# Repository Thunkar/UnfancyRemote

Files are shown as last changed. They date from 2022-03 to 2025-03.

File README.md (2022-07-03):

# The Unfancy Remote

A cheap, open, modular and reliable DIY remote with a focus on RF performance. 

**WARNING** : The software and CAD files included in this repo are in a **BETA STAGE** at the moment and **SHOULD BE USED CAREFULLY**. I am not responsible for **ANY** injures or damages you may incur as a result of using the HW or SW described in this project.

# Design considerations

* Unfancy. I use other devices for my telemetry, so no UART (even though could be easily added in the future) or OLED screens. PPM for the win.
* DIY friendly and modular. 
* Stellar RF performance is a must. The whole idea for this project came after in the FPV drone space [this project](https://www.expresslrs.org/2.0/) became super popular. It uses LoRa transcievers to achieve great range and link speeds, using a proprietary modulation that is specially robust against interference. It can also work on 433MHz/868MHz/2.4GHz bands depending on the specific module.
* Multiple shells to accomodate thumbwheels, triggers, Qi charging, battery sizes...
* Community driven

# Building the code

It has been tested on the latest (at the time of writing, 1.8.19) Arduino IDE version, using the fantastic [SX12XX Library](https://github.com/StuartsProjects/SX12XX-LoRa) by StuartsProjects.

# Documentation

1) [Ordering](./docs/ordering.md)
2) [Soldering](./docs/soldering.md)
3) [Assembly](./docs/assembly.md)
4) [Software configuration](./docs/software.md)
5) [Remote operation](./docs/operation.md)

# Contributing

All contributions must go through a process of review and validation via a Pull Request before being integrated into the codebase. If you wish to contribute, please fork the repo, perform your modifications **TEST THEM** and submit a PR for review. The place to discuss bugs, new features or suggestions is the [esk8 news forum](https://forum.esk8.news/t/the-unfancy-remote-wip-diy-reliable-remote).

# License 
```
            DO WHAT THE FUCK YOU WANT TO PUBLIC LICENSE
                    Version 2, December 2004
 
 Copyright (C) 2022 Gregorio Juliana Quirós
  Madrid, Spain
 Everyone is permitted to copy and distribute verbatim or modified
 copies of this license document, and changing it is allowed as long
 as the name is changed.
 
            DO WHAT THE FUCK YOU WANT TO PUBLIC LICENSE
   TERMS AND CONDITIONS FOR COPYING, DISTRIBUTION AND MODIFICATION
 
  0. You just DO WHAT THE FUCK YOU WANT TO.
  ```

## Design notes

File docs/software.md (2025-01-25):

# Software configuration

## Download the Arduino software and required library

In order to do that, go to https://www.arduino.cc/en/software and get the appropriate version for your OS. Then, navigate to [this repo](https://github.com/StuartsProjects/SX12XX-LoRa) and download it as a `.zip` file:

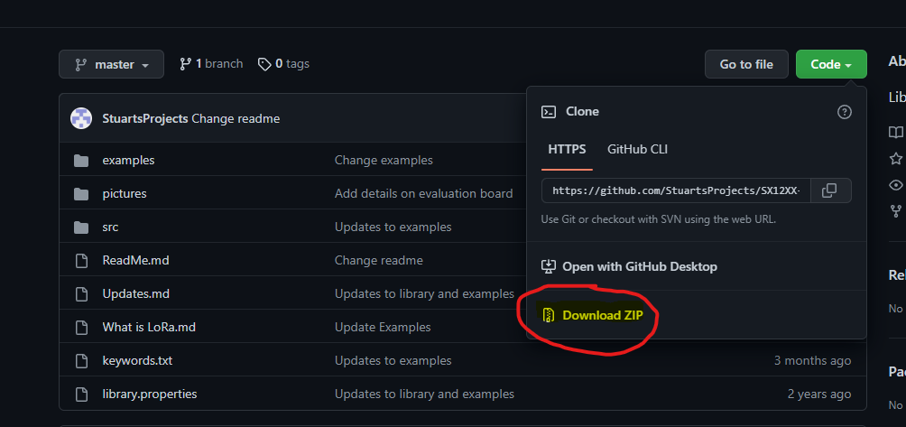
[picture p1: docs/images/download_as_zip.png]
Download as zip


Once you have it secured, import it in your arduino environment using the option `sketch->include library->add .zip library`

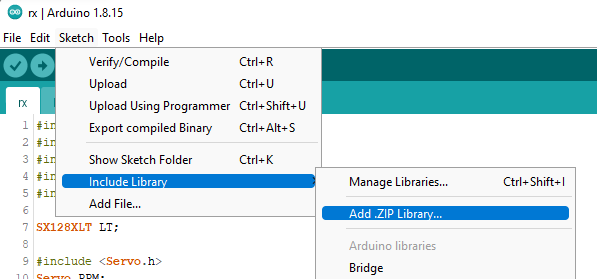
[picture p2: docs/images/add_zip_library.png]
Include zip library


Do the same for https://github.com/ednieuw/ESPAsyncWebServer.git

## Installing drivers for the USB-to-serial converter

If you're using windows, chances are you'll need to install [these drivers](https://ftdichip.com/drivers/)

## Configuring and flashing your transmitter

Download this repository using the same option you used to download the library. Once you have it unzipped, navigate to `software/tx`. The only file that should be modified in 99% of cases is `settings.h`. Configuration options are explained here:

```c
//#define DUAL_THROTTLE <- Uncomment this line if you're using a dual trigger case with 2 sensors.

// In case a dual trigger remote is used, the following line adjusts the sensitivity of the brakes, or in other words, when does the brake lever overrules the throttle. It is NOT recommended to lower it, but it can be raised to prevent accidental brake activation

#ifdef DUAL_THROTTLE
const float BRAKE_SENSITIVITY = 5; 
#endif

// Pairing: Choose a channel (0-40) and a transmitter identity (0-254) to prevent collisions with nearby remotes or other LoRa devices. These numbers must match the receiver's.

const unsigned int channel = -1;
const unsigned int TXIdentity = -1; 

// Battery levels: VREF is the actual internal reference of the Arduino, that can differ from one board to another. It can be adjusted here, increasing this number if the battery is reading high or decreasing it if it's reading low. It is strongly encouraged to use a multimeter to verify the actual values.

const unsigned long VREF = 1148566;

// Battery thresholds: Define what each LED of the remote means in terms of cell voltage, both for the remote and the board. First level is 4 LEDs ON, second one 3, etc. The last level will make the remote rumble and the last LED blink. WARNING: a maximum board voltage of 12S (50.4V) is measurable.

const float REMOTE_BATTERY_CELL_V_THR[] = { 4.0, 3.8, 3.7, 3.5, 3.3 };

const float BOARD_BATTERY_CELL_V_THR[] = { 4.0, 3.8, 3.7, 3.5, 3.3 };
const unsigned int BOARD_CELL_S = 12;

```

Once configured, connect the board to the usb adapter. The 328p based boards use this orientation with the jumper on the 3.3V position:

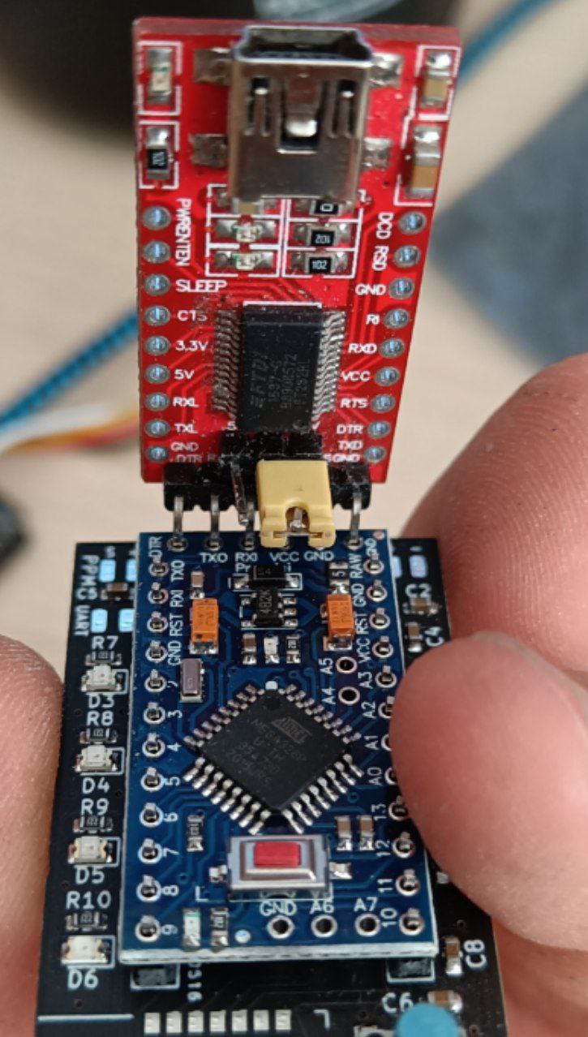
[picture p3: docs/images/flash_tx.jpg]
Flash tx


Select the appropriate board and port in the Arduino IDE:

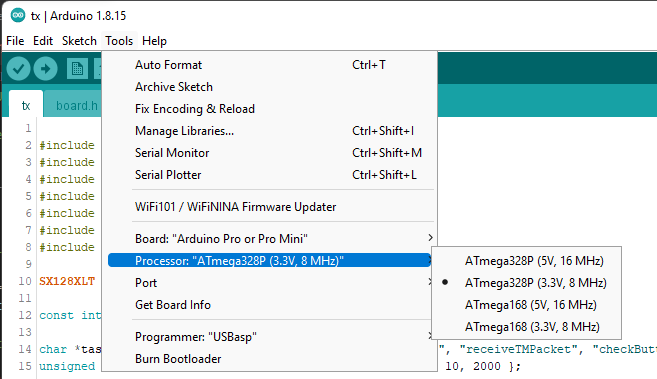
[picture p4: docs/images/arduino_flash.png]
Arduino flash


And upload the code using the upload button (`sketch->upload`). 

## Calibration

If everything worked correctly, the remote should perform the startup routine (rumble + 4 LED on in sequence) and start the calibration routine (1 LED on). To calibrate the remote, follow these steps:

* Don't touch the thumbwheel/triggers to perform center detection. Click the button once.
* Second LED should light up. Push the thumbwheel/acceleration trigger to the maximum acceleration position and let it return to center. Click the button once.
* Third LED should light up. Push the thumbwheel/brake trigger to the maximum braking position and let it return to center. Click the button once.
* The fourth LED should light up and then all of them turn off. Calibration is complete.

After you're finished, it'll start to output debugging information through the serial port running at 115200 baud.

## Configuring and flashing the receiver

Similarly, the receiver has to be configured with matching pairing info:

```c
// Pairing: Choose a channel (0-40) and a transmitter identity (0-254) to prevent collisions with nearby remotes or other LoRa devices. These numbers must match the transmitter's.

const unsigned int channel = -1;
const unsigned int RXIdentity = -1; 

// Battery levels: VREF is the actual internal reference of the Arduino, that can differ from one board to another. It can be adjusted here, increasing this number if the battery is reading high or decreasing it if it's reading low. It is strongly encouraged to use a multimeter to verify the actual values.

const unsigned long VREF = 1148566;
```

And flashed taking into account the board type. Ff you're using a 168 equipped board, chose it accordingly in the IDE and make sure you connect the adapter correctly:

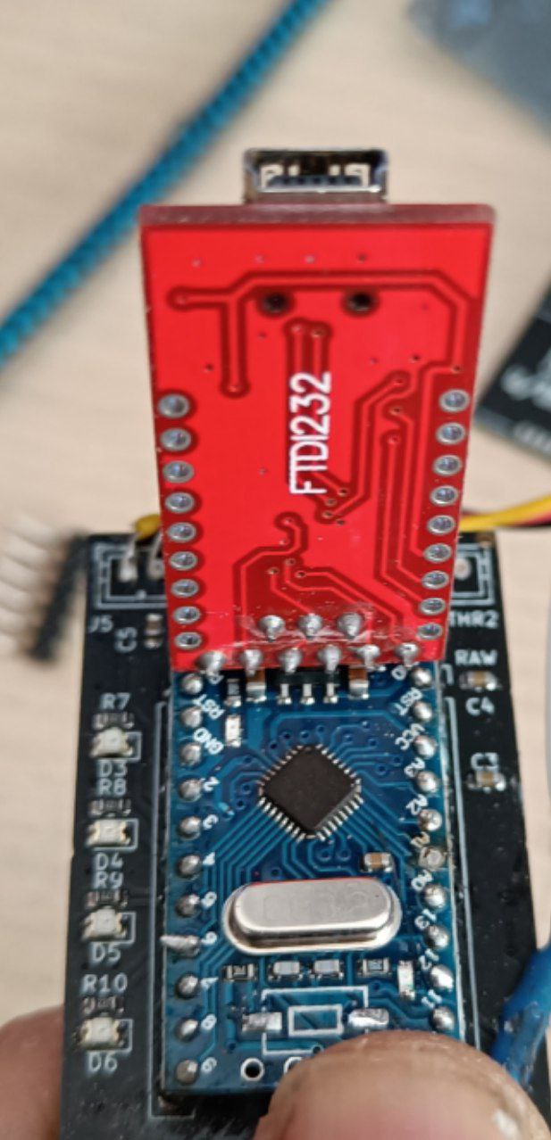
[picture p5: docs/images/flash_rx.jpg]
Flash rx


## Making sure it worked

Turn on the transmitter and connect the receiver to the USB adapter. Using the serial monitor, verify that the receiver is receiving approx. 50 throttle packages per second (usually 47-49) and is emitting 2 TM packages per second (some can be lost, is not a big deal).

## Connecting the receiver to the board

Depending on the ESC you're using the communications port can be arranged in a number of ways, but bear in mind the receiver requires 5V to work. If you want to have battery monitoring for your board in the remote, make sure to take a cable directly from the positive end of your battery and solder it to the VBAT pad in the receiver.

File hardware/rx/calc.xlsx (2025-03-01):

Ref
4.2
Cells | Voltages | R1 | R2 | Max Ouptut | Leakage current (mA)
12 | 50.4 | 100000 | 5600 | 2.672727273 | 0.4772727273
14 | 58.8 | 100000 | 4700 | 2.639541547 | 0.5616045845
16 | 67.2 | 120000 | 4700 | 2.532798717 | 0.538893344
18 | 75.6 | 120000 | 3300 | 2.023357664 | 0.6131386861
20 | 84 | 150000 | 4700 | 2.552036199 | 0.5429864253
22 | 92.4 | 150000 | 3300 | 1.989041096 | 0.602739726

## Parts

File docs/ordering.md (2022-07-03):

# Ordering

## PCBs

Ordering from [JLCPCB](https://jlcpcb.com/) is very easy. First of all, make sure you have successfully downloaded or cloned this repository in your computer, and have unzipped the contents. The first step is to go to the website and click on 'Add gerber file':

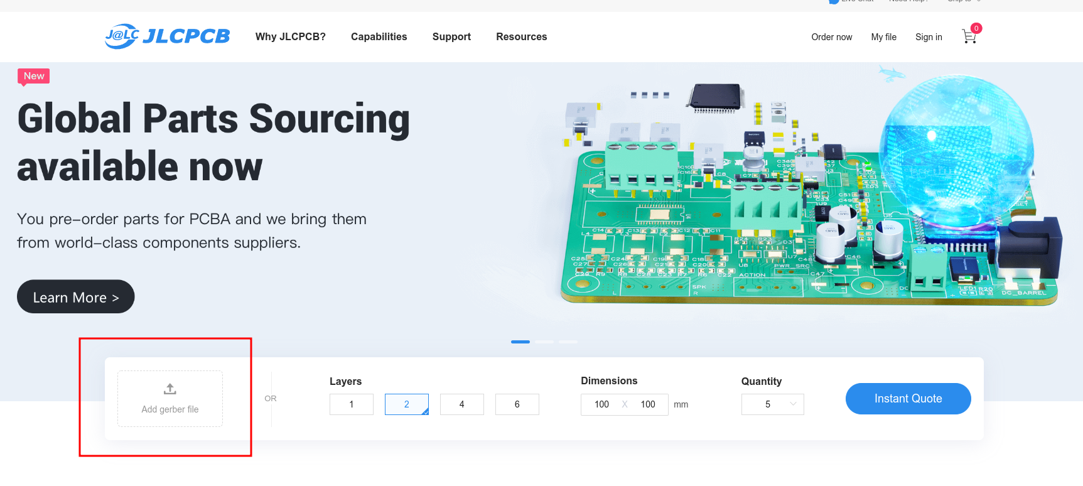
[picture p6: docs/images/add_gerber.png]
Add gerber


Then navigate to `hardware/jlcpcb/gerber` and select `GERBER-unfancyRemote.zip`. These are the design files for the boards that tell the manufacturer exactly how to make them (copper, silkscreen, vias, holes, etc). Once they're loaded and analyzed, you should select the following manufacturing options, except color which you can choose (as long as JLCPB supports SMD assembly in that particular color). The price per remote goes way down if you order 20+ boards, and you need 2 per kit (1 transmitter and 1 receiver, the same PCB can act as both). Get some friends to join your purchase!

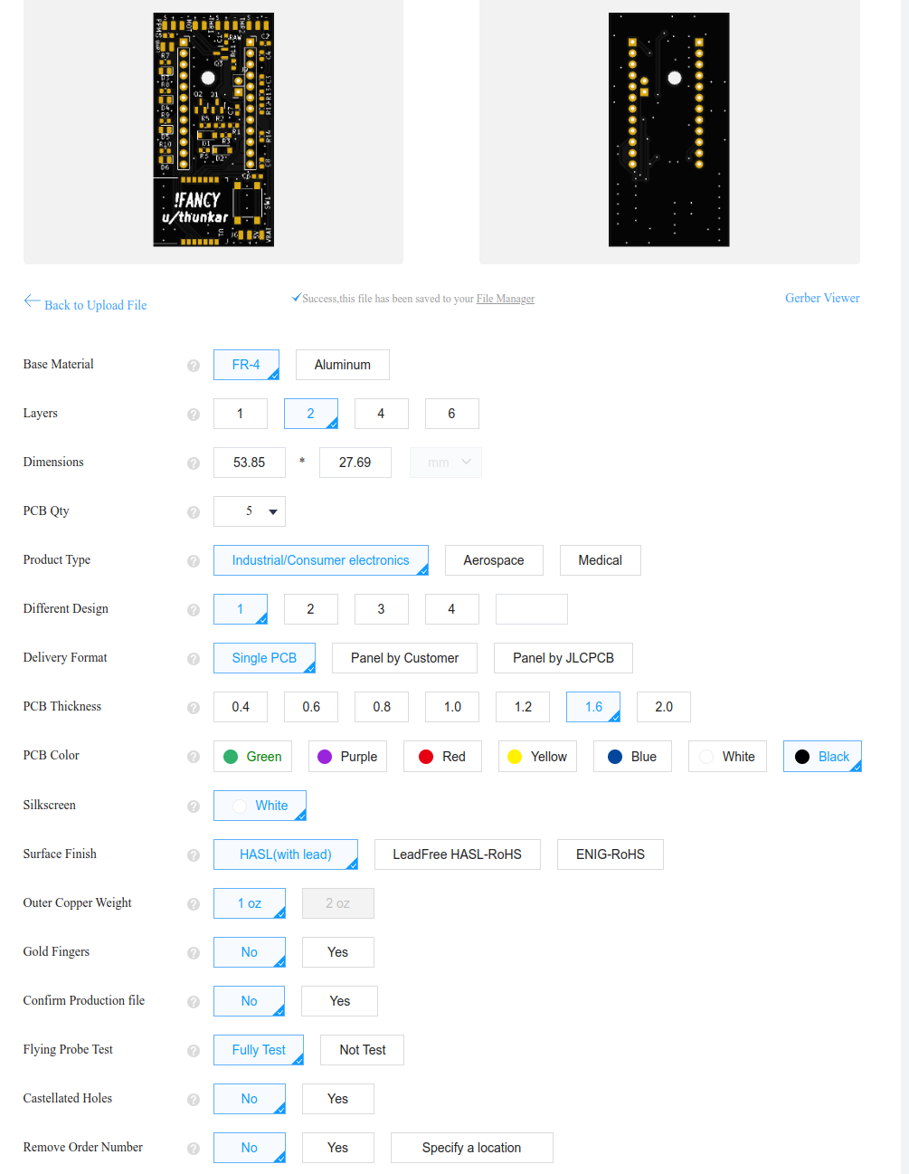
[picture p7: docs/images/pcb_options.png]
PCB options


Select "PCB assembly" and the following options. The PCB only has components on the top side, so manual soldering will be kept to a minimum:

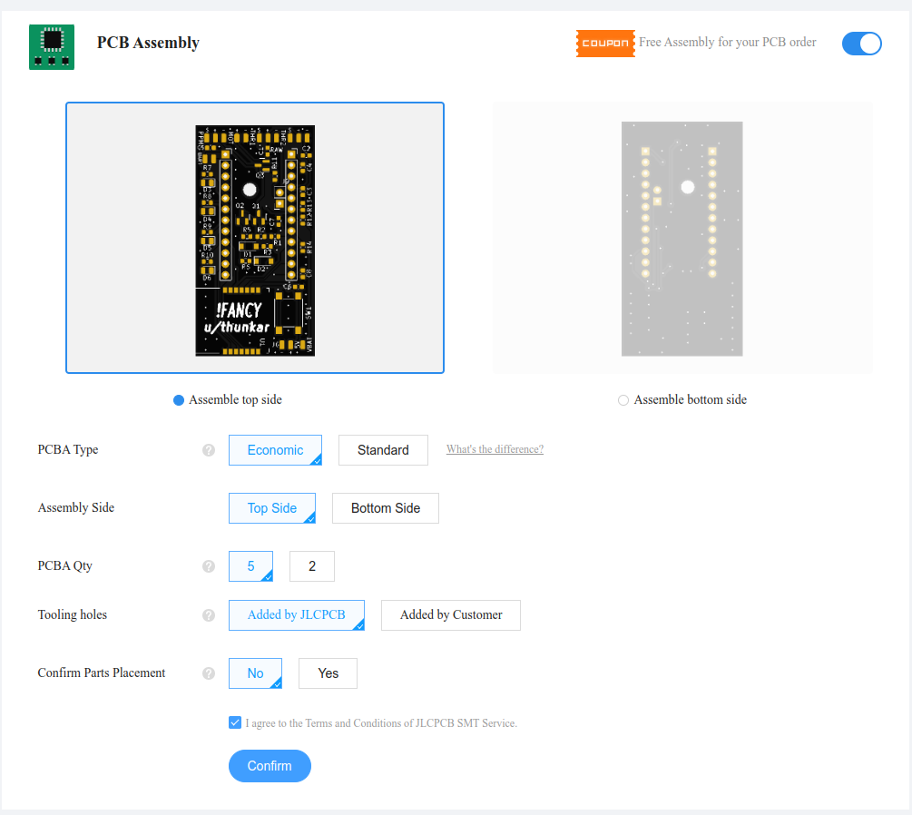
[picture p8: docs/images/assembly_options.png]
PCB assembly


On the next screen, upload the BOM (`hardware/jlcpcb/assembly/BOM-unfancyRemote.csv`) and CPL file (`hardware/jlcpcb/assembly/POS-unfancyRemote.csv`). Select `Research/Education/DIY/Entertainment -> Toy` as category and click next. The component list should appear, leaving only 3 unpopulated parts: Arduino digital, Arduino analog and Extra analog 1. This is fine, you'll solder this when assembling the remote. If there are more components missing, create a [PR](https://github.com/Thunkar/UnfancyRemote/pulls) so we can try and find an alternative.

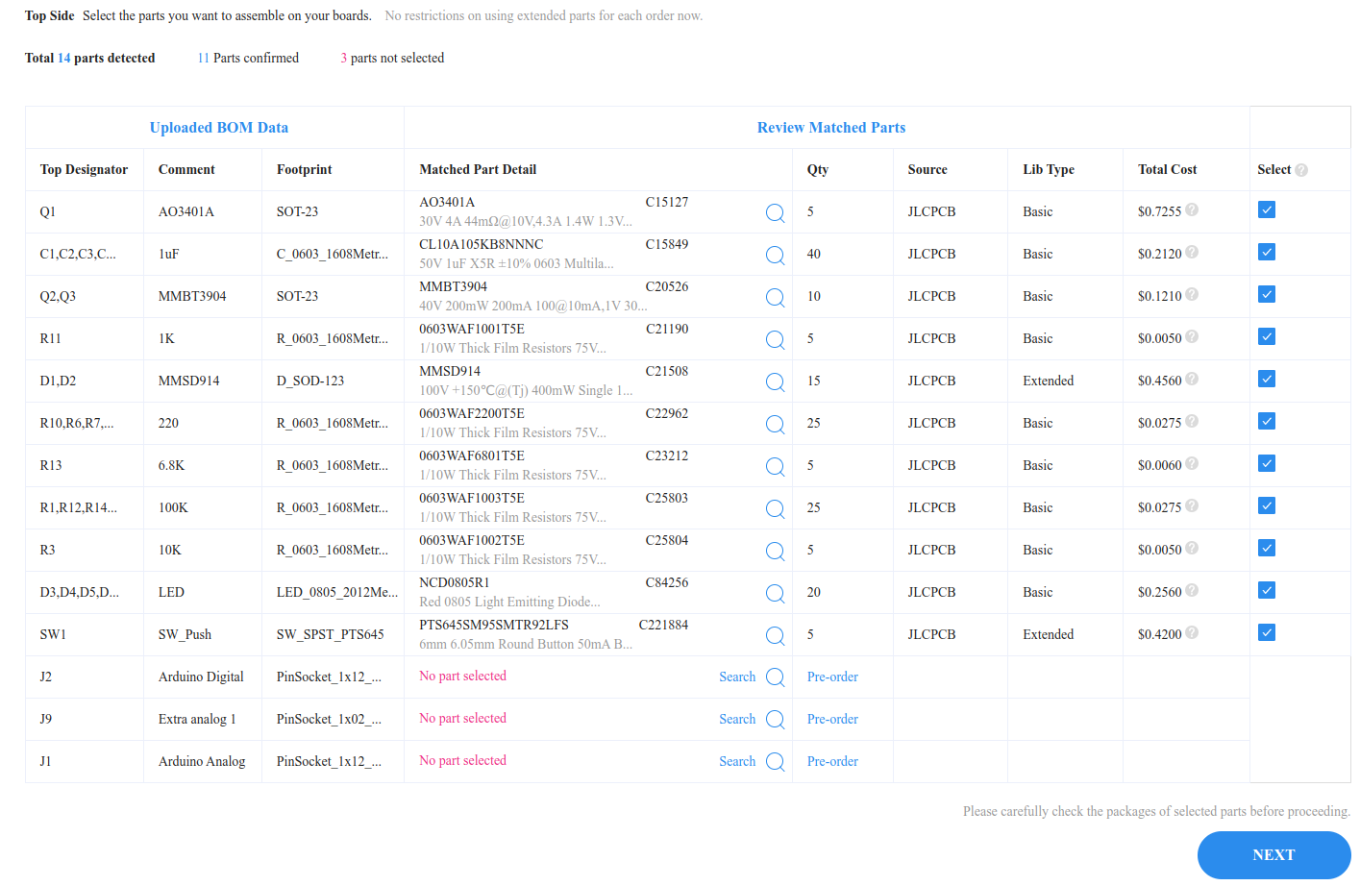
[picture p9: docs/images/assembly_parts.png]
Assembly parts


Next you'll see a summary of your order. Pricing should be around $20 excluding shipping if you select only 5 PCBs, but I do insist that 20 will be less than $50 WITH shipping, so find some mates! In the unselected parts section only headers/connectors and the LoRa module should appear:

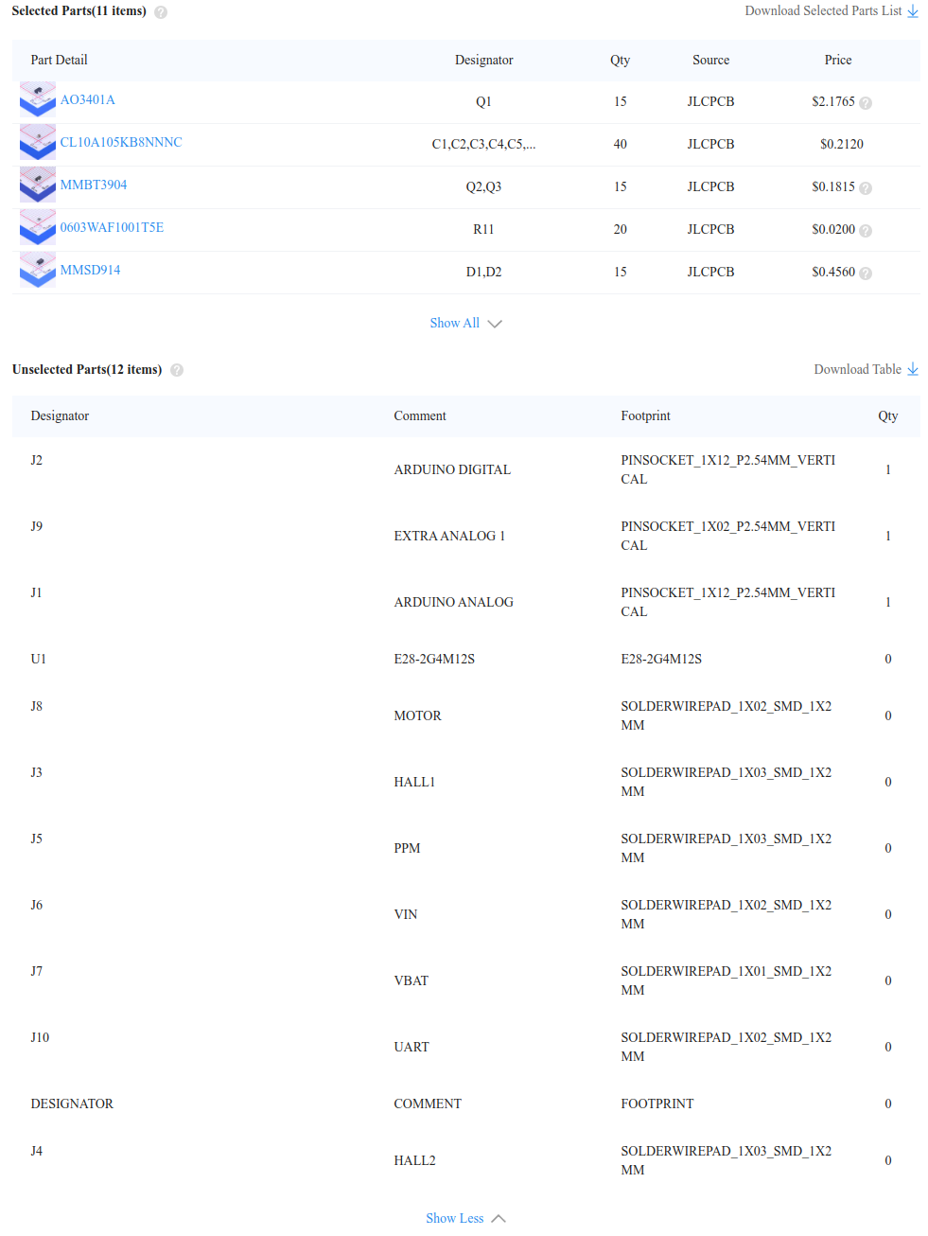
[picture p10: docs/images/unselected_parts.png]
Unselected parts


You're done! Pay for your order and shipping, it should be with you in less than 15 days even with the cheapest option.

## Other components

| Part | Description | Required quantity | Aliexpress | Amazon (ES) |
| --- | --- | --- | --- | --- |
| Springs | 20x5x0.5 (length\*inner diameter\*wire diameter). 0.4/0.6 wire diameter could work for softer/stiffer | 1 (2 for dual trigger) | [Link for 10 springs](https://es.aliexpress.com/item/1005003435808058.html) | [Kit with a lot of springs, not recommended](https://www.amazon.es/gp/product/B01KG024CU/ref=ppx_yo_dt_b_asin_title_o05_s00) |
| E28-2G4M12S SX1280 2.4G LoRa Module | One for the remote, another for the receiver | 2 | [Single module](https://es.aliexpress.com/item/1005003949324557.html) | [Single module](https://es.aliexpress.com/item/1005003949324557.html) |
| Arduino Pro Mini 3.3V 8MHz Atmega 328P | Required for the remote ATM, can be also used in the receiver but it's more expensive | 1 (2 if used also in the receiver) | [Single board](https://es.aliexpress.com/item/4000873049870.html?spm=a2g0o.order_list.0.0.35de194dDIWxKm&gatewayAdapt=glo2esp) | [Single board](https://www.amazon.es/gp/product/B01DUSDQQ8/ref=ppx_yo_dt_b_asin_title_o02_s00?ie=UTF8&psc=1) |
| Arduino Pro Mini 3.3V 8MHz Atmega 168  | Can be used in the receiver as cheaper alternative | 1 (if not using 2x 328P) | [Single board](https://es.aliexpress.com/item/4000873049870.html?spm=a2g0o.order_list.0.0.35de194dDIWxKm&gatewayAdapt=glo2esp) | N/A 
| Serial to USB adapter | Used to upload FW to the Arduino | 1 | [1 board](https://es.aliexpress.com/item/32460118879.html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) | [1 board](https://www.amazon.es/Movilideas-Adaptador-FT232RL-Serie-Arduino/dp/B07H9CXVGK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) |
| LiPo charger | Micro USB, pretty inexpensive | 1 | [10 boards](https://es.aliexpress.com/item/1800678916.html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) | [1-3-5 boards](https://www.amazon.es/gp/product/B07D2G345P/ref=ppx_yo_dt_b_asin_title_o05_s00?ie=UTF8&psc=1) |
| 3.0-4.2 to 5V regulator | From battery voltage to 5V, extremely small (audible coil whine) | 1 | [5 boards](https://es.aliexpress.com/item/4000805939587.html?spm=a2g0o.order_list.0.0.1024194dNATUMn&gatewayAdapt=glo2esp) | N/A |
| LiPo battery | Bought Tattu LiPos a while back and they're good. Cannot vouch for aliexpress ones | 1 | [Pick your poison, any of this size works](https://es.aliexpress.com/item/1005001330075053.html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) | [6 batteries](https://www.amazon.es/gp/product/B07X9XYPP5/ref=ppx_yo_dt_b_asin_title_o09_s00?ie=UTF8&psc=1) |
| Magnets | 4x2 (diameter\*height) N35 neodymium magnets | 2 | [50 pack](https://es.aliexpress.com/item/1005002803855055.html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) | [50 pack](https://www.amazon.es/gp/product/B00TACMJEO/ref=ppx_yo_dt_b_search_asin_title?ie=UTF8&psc=1) |
| Hall sensor | 49E linear hall sensor (SS49E) | 1 (2 for dual trigger) | [10 pack](https://es.aliexpress.com/item/32590021901.html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) | [10 pack](https://www.amazon.es/gp/product/B08LD57DZ6/ref=ppx_yo_dt_b_asin_title_o00_s00?ie=UTF8&psc=1) |
| Bearing | MR148ZZ ball bearing | 1 (2 for dual trigger) | [10 pack](https://es.aliexpress.com/item/32834754915.html?spm=a2g0o.order_list.0.0.35de194dDIWxKm&gatewayAdapt=glo2esp) | N/A |
| Qi Charger | OPTIONAL. But very cool (pick the round antenna, blue PCB version) | 1 | [Single board](https://es.aliexpress.com/item/1005003411188792.html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) | N/A |
| Vibration motor | Technically optional but highly recommended | 1 | [10 motors](https://es.aliexpress.com/item/4000245243914.html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) | [5 motors](https://www.amazon.es/gp/product/B0839H19HY/ref=ppx_yo_dt_b_asin_title_o06_s00?ie=UTF8&psc=1) |
| Lanyard | Any would do, really | 1 | [1 lanyard](https://es.aliexpress.com/item/1005001914422530.html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) | N/A 
| Brass inserts | M3x4 (short) | 6 | [100 pack](https://es.aliexpress.com/item/1005002069529871.html) | [100 pack](https://www.amazon.es/gp/product/B09ZHSGHXD/ref=ppx_yo_dt_b_asin_title_o05_s00?ie=UTF8&th=1) |

I'll try to keep this updated if I find better options. If you do, please open a [PR](https://github.com/Thunkar/UnfancyRemote/pulls)

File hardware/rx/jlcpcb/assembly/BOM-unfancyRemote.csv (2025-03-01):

Comment | Designator | Footprint | LCSC
AO3401A | Q1 | SOT-23 | C15127
1uF | C1,C2,C3,C4,C5,C6,C7,C8 | C_0603_1608Metric | C15849
MMBT3904 | Q2,Q3 | SOT-23 | C20526
1K | R11 | R_0603_1608Metric | C21190
MMSD914 | D1,D2 | D_SOD-123 | C21508
SW_Push | SW1 | SW_SPST_PTS645 | C221884
220 | R10,R6,R7,R8,R9 | R_0603_1608Metric | C22962
6.8K | R13 | R_0603_1608Metric | C23212
100K | R1,R12,R14,R2,R5 | R_0603_1608Metric | C25803
10K | R3 | R_0603_1608Metric | C25804
LED | D3,D4,D5,D6 | LED_0805_2012Metric | C84256
Arduino Digital | J2 | PinSocket_1x12_P2.54mm_Vertical
E28-2G4M12S | U1 | E28-2G4M12S
Arduino Analog | J1 | PinSocket_1x12_P2.54mm_Vertical
VIN | J6 | SolderWirePad_1x02_SMD_1x2mm
HALL1 | J3 | SolderWirePad_1x03_SMD_1x2mm
HALL2 | J4 | SolderWirePad_1x03_SMD_1x2mm
PPM | J5 | SolderWirePad_1x03_SMD_1x2mm
Extra analog 1 | J9 | PinSocket_1x02_P2.54mm_Vertical
Motor | J8 | SolderWirePad_1x02_SMD_1x2mm
VBAT | J7 | SolderWirePad_1x01_SMD_1x2mm
UART | J10 | SolderWirePad_1x02_SMD_1x2mm

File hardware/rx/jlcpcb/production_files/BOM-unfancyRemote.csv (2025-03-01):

Comment | Designator | Footprint | LCSC | Quantity
TPS61085DGK | U4 | VSSOP-8_3x3mm_P0.65mm | C113659 | 1
1K | R11,R16,RT1 | R_0402_1005Metric | C11702 | 3
10uF | C11,C13,C14,C6,C8 | CP_EIA-3216-10_Kemet-I | C119051 | 5
4.7uF | C10,C9 | CP_EIA-3216-10_Kemet-I | C123256 | 2
MCP73871-2AA | U2 | QFN-20-1EP_4x4mm_P0.5mm_EP2.5x2.5mm | C144351 | 1
MMBT3904 | Q2,Q3 | SOT-23 | C20526 | 2
MMSD914 | D1,D2 | D_SOD-123 | C21508 | 2
220 | R6 | R_0402_1005Metric | C25091 | 1
470 | R15,R4,R7 | R_0402_1005Metric | C25117 | 3
100K | R1,R12,R14,R2,R5 | R_0402_1005Metric | C25741 | 5
10K | R17,R3 | R_0402_1005Metric | C25744 | 2
18.2K | R18 | R_0402_1005Metric | C25859 | 1
27K | R20 | R_0402_1005Metric | C284471 | 1
MIC5219-3.3YM5 | U5 | SOT-23-5 | C29613 | 1
100nF | C16 | C_0402_1005Metric | C307331 | 1
SW_Push | SW1 | SW_SPST_PTS645 | C393947 | 1
6.8K | R13 | R_0402_1005Metric | C407725 | 1
150K | RT2 | R_0402_1005Metric | C407748 | 1
D_Schottky | D9 | D_SOD-523 | C413992 | 1
1.6nF | C7 | C_0603_1608Metric | C437532 | 1
68K | R19 | R_0402_1005Metric | C482226 | 1
1uF | C12,C15 | C_0402_1005Metric | C52923 | 2
3.3uH | L1 | L_Cenker_CKCS201610 | C696469 | 1
10K | TH1 | R_0402_1005Metric | C700818 | 1
AO3401A | Q1 | SOT-23 | C700954 | 1
LED | D3,D7,D8 | LED_0805_2012Metric | C84256 | 3
WS2812B | D10,D4,D5,D6 | LED_WS2812B-2020_PLCC4_2.0x2.0mm | C965555 | 4
E28-2G4M12S | U1 | E28-2G4M12S |  | 1
Battery | J1 | PinHeader_1x02_P2.00mm_Vertical |  | 1
VIN | J6 | SolderWirePad_1x02_SMD_1x2mm |  | 1
HALL1/PPM | J3 | SolderWirePad_1x03_SMD_1x2mm |  | 1
HALL2 | J4 | SolderWirePad_1x03_SMD_1x2mm |  | 1
Motor | J8 | SolderWirePad_1x02_SMD_1x2mm |  | 1
ESP32-C3_SUPERMINI | U3 | MODULE_ESP32-C3_SUPERMINI |  | 1

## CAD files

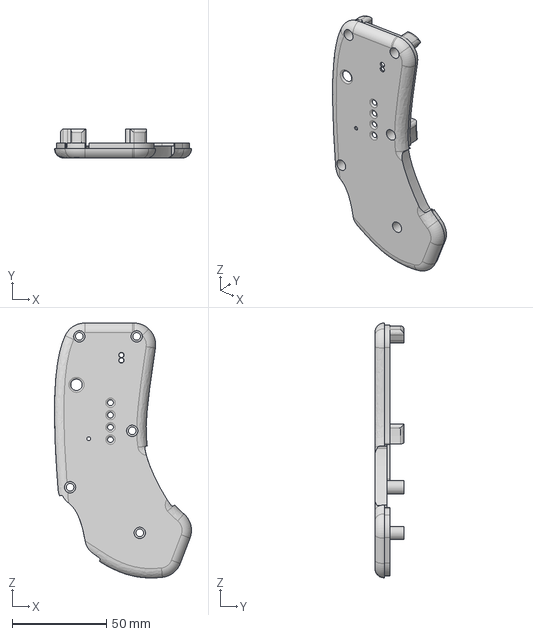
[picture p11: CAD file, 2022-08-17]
cad/dualTrigger/dualTriggerTop.step
72.5 x 15.5 x 134.9 mm

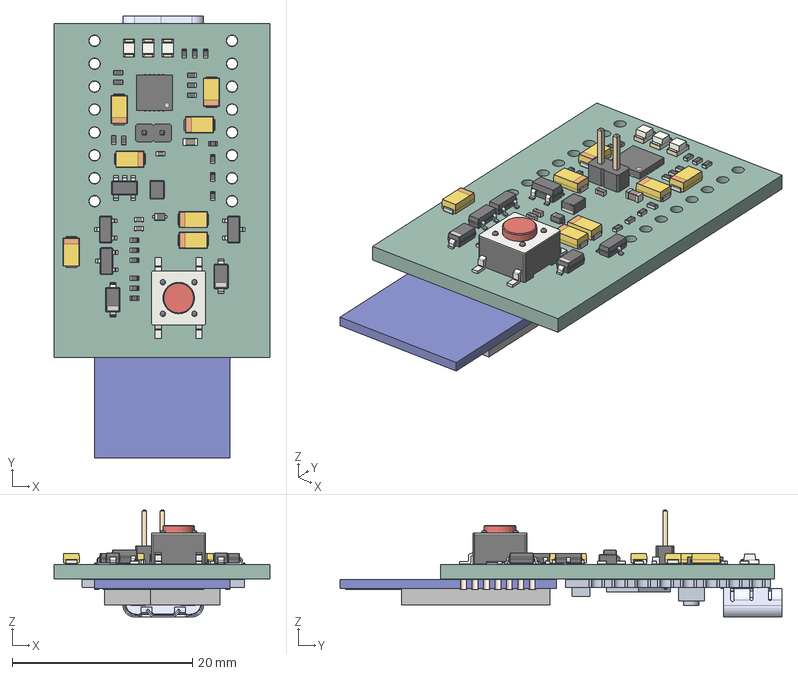
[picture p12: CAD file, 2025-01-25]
cad/misc/PCBv3.step
23.9 x 49.0 x 11.9 mm
R_0402_1005Metric x 20
SOT_23_5
C_0402_1005Metric x 3
CP_EIA_3216_10_Kemet_I x 7
QFN-20-1EP_4x4mm_Pitch0.5mm
L_Cenker_CKCS201610
D_SOD_123 x 2
PinHeader_1x02_P200mm_Vertical
D_SOD_523
LED_0805_2012Metric x 3
SOT_23 x 3
C_0603_1608Metric
SW_SPST_PTS645
E28-2G4M12S v2
ESP32-C3 SuperMini
unfancyRemote_PCB

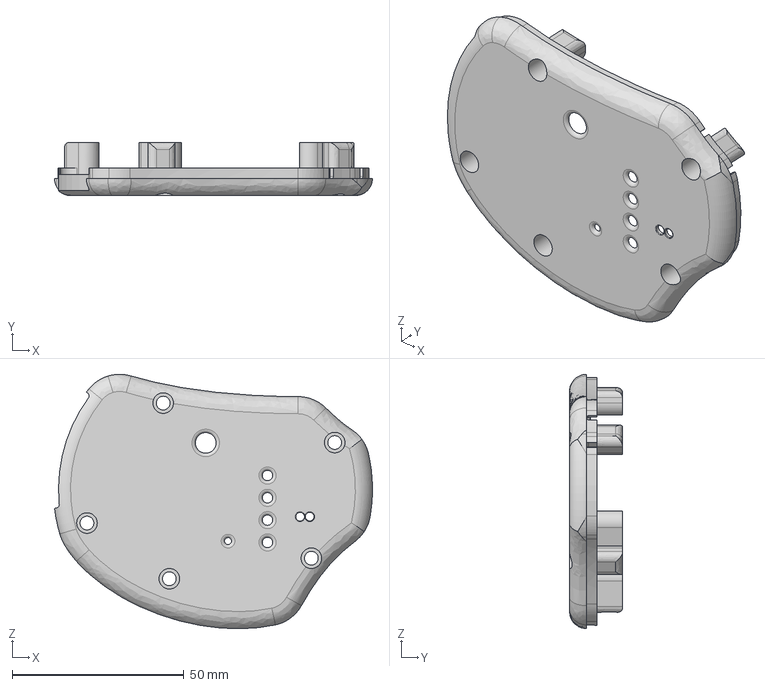
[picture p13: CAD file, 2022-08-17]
cad/round/roundTop.step
92.7 x 15.5 x 74.1 mm

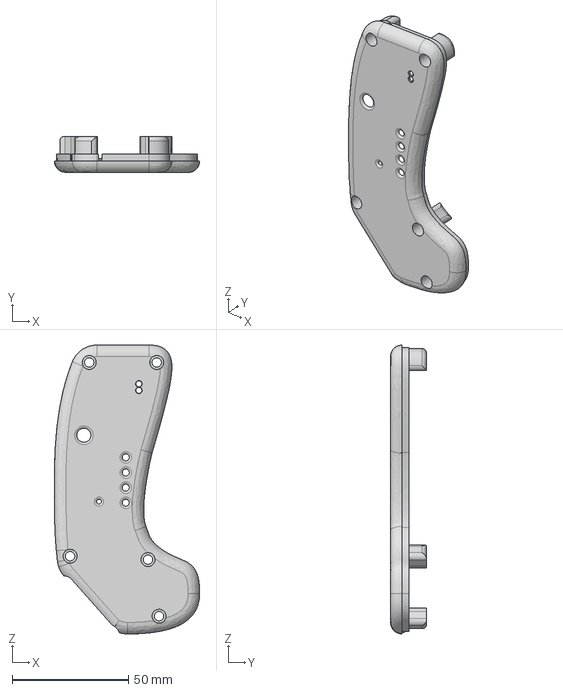
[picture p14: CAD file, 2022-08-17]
cad/thumbwheel/thumbwheelTop.step
62.5 x 15.5 x 124.2 mm

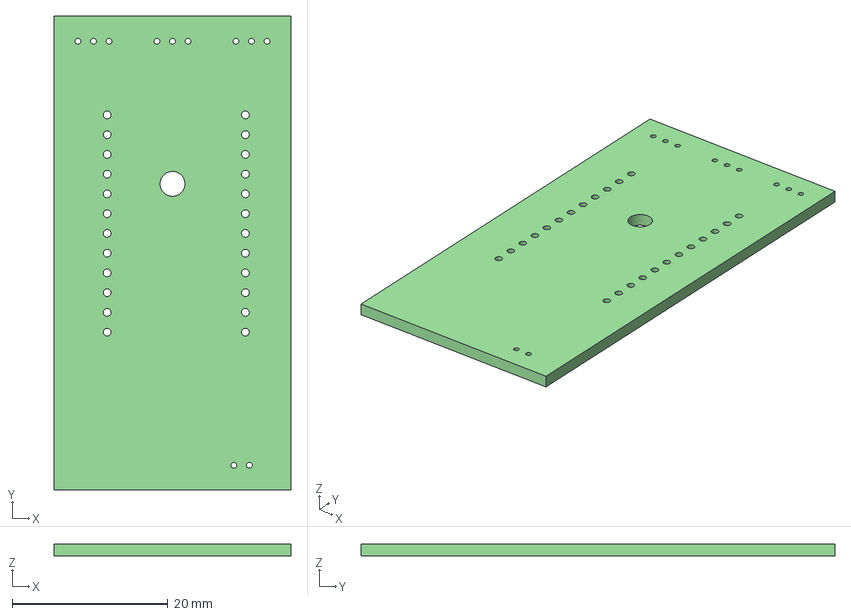
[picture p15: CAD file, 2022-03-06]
hardware/rx/rx.step
30.5 x 61.0 x 1.60 mm

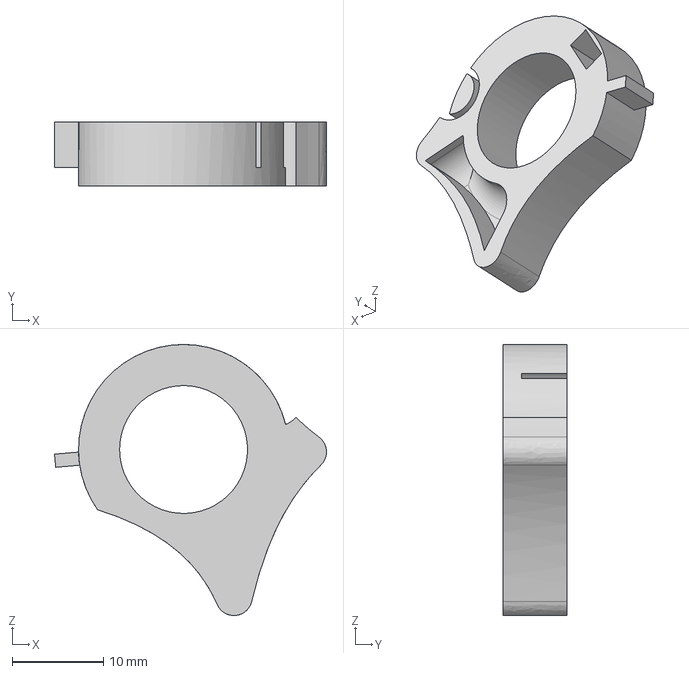
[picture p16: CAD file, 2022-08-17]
cad/dualTrigger/reverseTrigger.step
29.8 x 7.00 x 29.7 mm

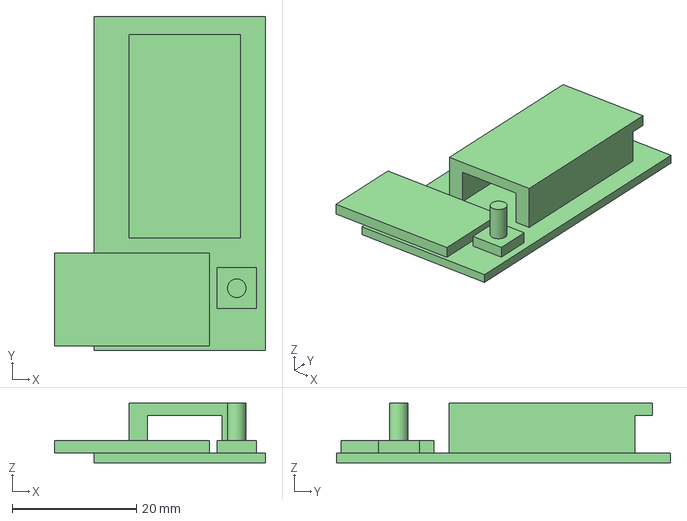
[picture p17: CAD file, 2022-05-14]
cad/misc/PCBv2.step
34.1 x 53.8 x 9.60 mm

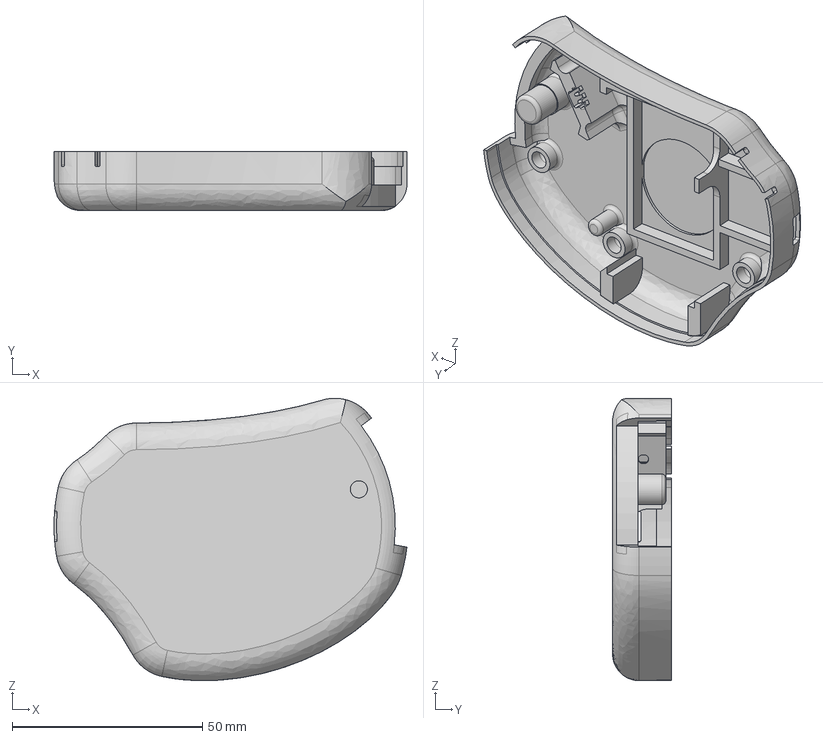
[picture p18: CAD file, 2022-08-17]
cad/round/roundBase.step
92.7 x 15.5 x 74.1 mm

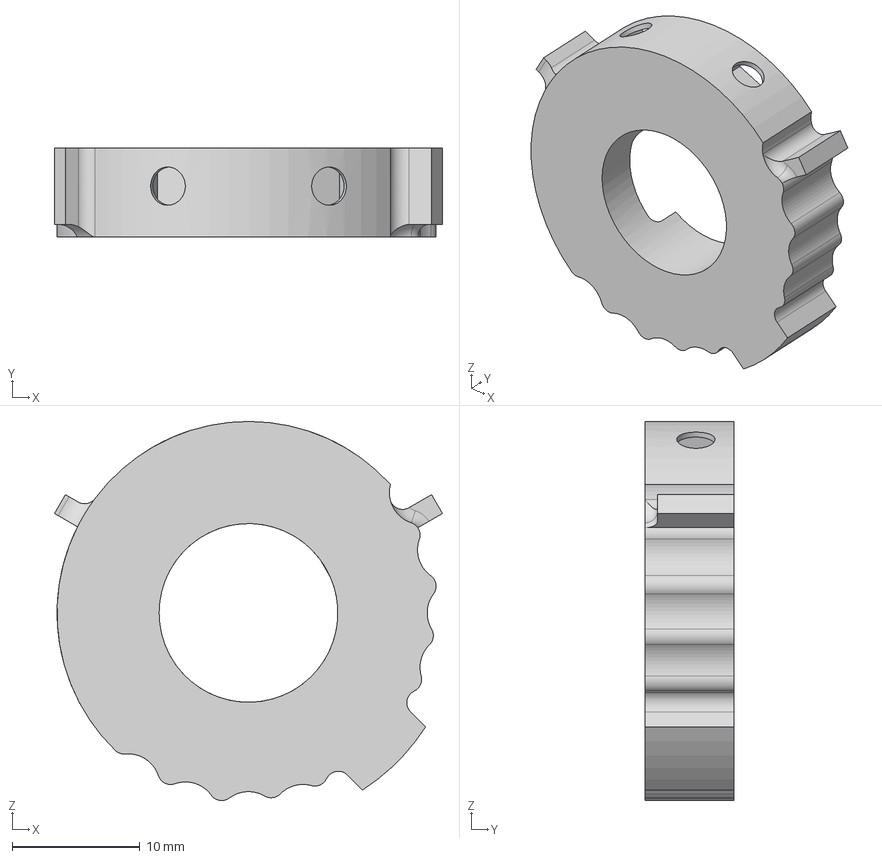
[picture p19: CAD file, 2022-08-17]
cad/thumbwheel/thumbwheelSmall.step
30.4 x 7.00 x 29.7 mm

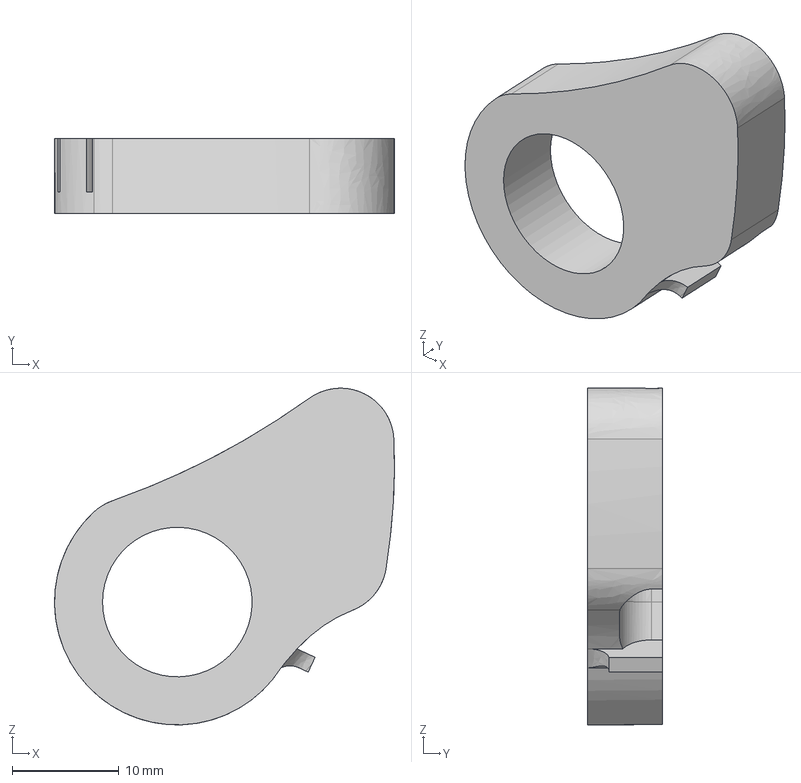
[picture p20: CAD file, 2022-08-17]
cad/dualTrigger/trigger.step
31.8 x 7.00 x 31.5 mm

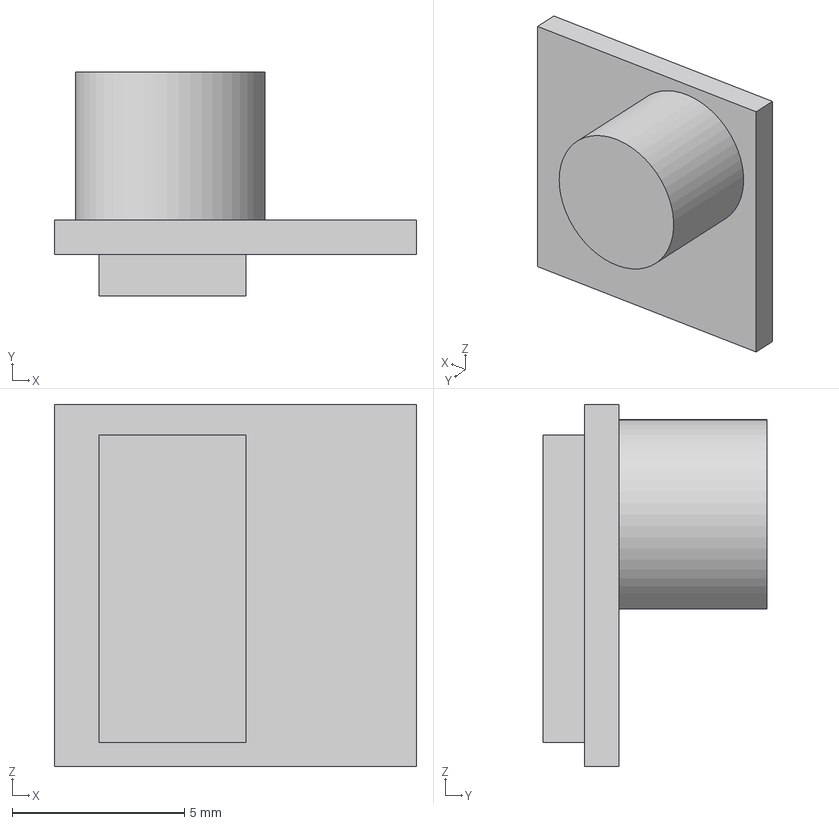
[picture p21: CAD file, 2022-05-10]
cad/misc/smallRegulator.step
10.5 x 6.50 x 10.5 mm

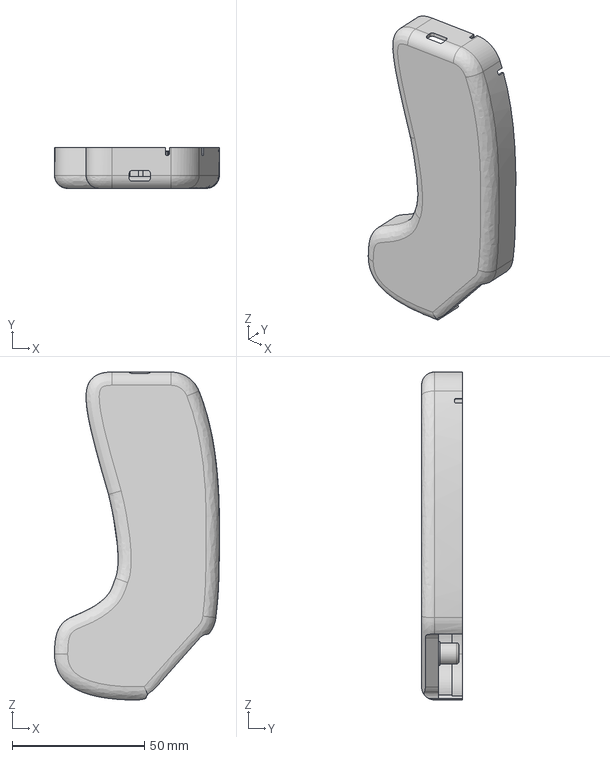
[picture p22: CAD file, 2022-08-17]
cad/thumbwheel/thumbwheelBase.step
62.5 x 15.5 x 124.2 mm

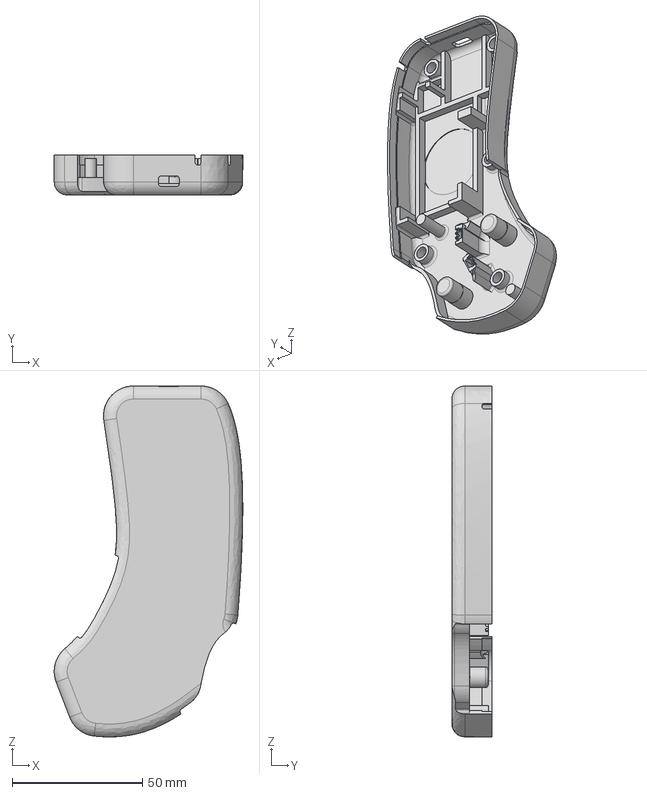
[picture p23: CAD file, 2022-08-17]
cad/dualTrigger/dualTriggerBase.step
72.5 x 15.5 x 134.9 mm

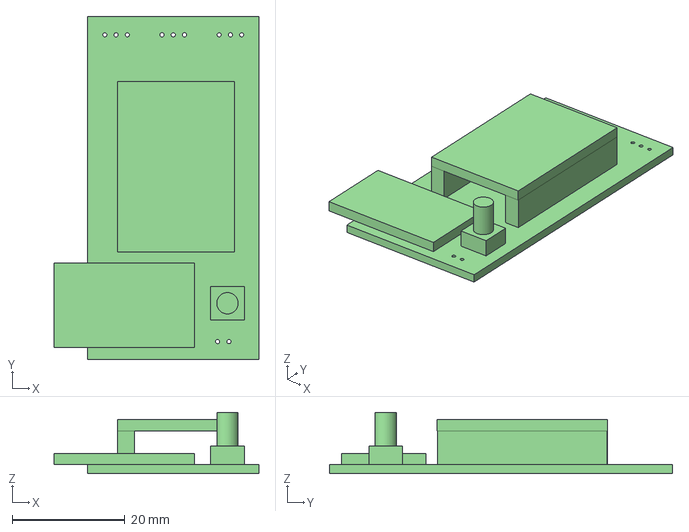
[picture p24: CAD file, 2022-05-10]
cad/misc/PCB.step
36.4 x 61.0 x 10.9 mm

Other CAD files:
cad/round/thumbwheelSmall.step
cad/round/roundTopAlt.step
cad/misc/smallBearing.step
cad/dualTrigger/dualTriggerBase.f3d
cad/dualTrigger/dualTriggerBase.stl
cad/dualTrigger/dualTriggerTop.f3d
cad/dualTrigger/dualTriggerTop.stl
cad/dualTrigger/reverseTrigger.f3d
cad/dualTrigger/reverseTrigger.stl
cad/dualTrigger/trigger.f3d
cad/dualTrigger/trigger.stl
cad/misc/PCB.f3d
cad/misc/PCBv2.f3d
cad/misc/battery.f3d
cad/misc/battery.step
cad/misc/charger.f3d
cad/misc/charger.step
cad/misc/smallBearing.f3d
cad/misc/smallRegulator.f3d
cad/round/hook.f3d
cad/round/hook.step
cad/round/hook.stl
cad/round/roundBase.f3d
cad/round/roundBase.stl
cad/round/roundBaseAlt.f3d
cad/round/roundBaseAlt.step
cad/round/roundBaseAlt.stl
cad/round/roundTop.f3d
cad/round/roundTop.stl
cad/round/roundTopAlt.f3d
cad/round/roundTopAlt.stl
cad/round/thumbwheelSmall.f3d
cad/round/thumbwheelSmall.stl
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

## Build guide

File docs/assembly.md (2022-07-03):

# Assembly

## 3D printing a case

It is recommended to print the remote case in a plastic meant for mechanical parts and capable of resisting some level of impact:

* PETG
* ABS
* Nylon
* ASA

I have personally tested PETG with great results, specially at 0.12mm layer height. 

## Putting it all together

The official cases have cutouts and walls designed to make sure every component is supported and doesn't move during operation. It is still recommended to secure them using double-sided sticky tape. As reference, a completely assembled round version is depicted below:

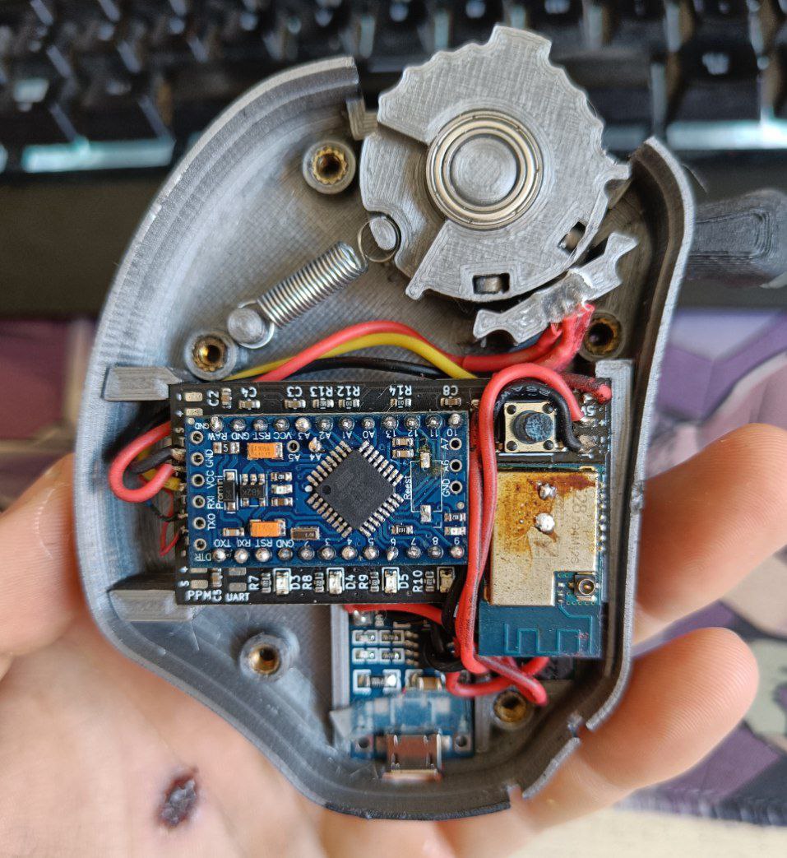
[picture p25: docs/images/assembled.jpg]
Assembled


## Moving parts

Triggers and thumbwheels are mounted on press fit ball bearings. If your printer tolerances are way off, a little bit of PTFE tape can be used to ensure a snug fit. The spring will be a little too tight when first assembled and also he friction will probably make it not return to center easily and completely. It is recommended to lube the cut where the spring is secured to the thumbwheel/trigger to ensure consistent centering, but a little bit of use will probably take care of it anyways.

## Sensor and magnets

For the thumbwheel versions make sure the magnets are configured facing opposite poles as follows: 

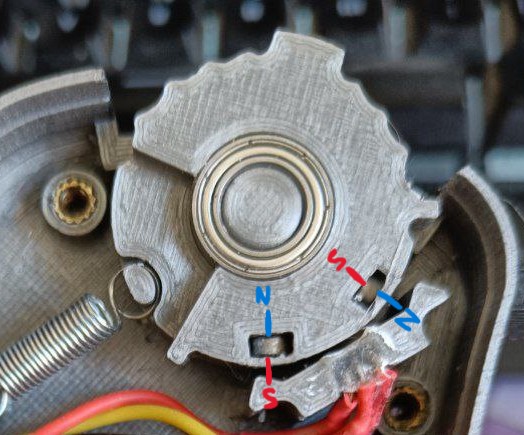
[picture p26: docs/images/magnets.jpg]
Magnets


It is ***NOT*** important which is the actual north or south pole of each magnet, ***JUST*** that they face opposite directions. The easiest way to accomplish this is to insert one of them and then make sure that it tries to *repel* the other one if you place it on the ouside of the wheel next to the already inserted one. 

Dual trigger version doesn't care about magnet orientation as they're two separate sensors that only use the unidirectional throw.

## **IMPORTANT**

Both the magnets and sensor should be glued in place once the setup is verified and working. Superglue or epoxy recommended.

## Inserts

The official cases use brass inserts to ensure the remote is closed up properly. They should be heated using a lighter and placed in the provided anchor points.

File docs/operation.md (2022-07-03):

# Operating the remote

Once assembled, configured with pairing information and connected, the remote should be configurable as any other PPM remote via the VESC tool. 

## Turning it on/off

To turn the remote on, press the button until it rumbles and ***ALL*** four LEDs turn on. Once they're all on, release the button. To turn it off, press the button for at least 5 seconds until it starts to rumble continuosly. Release the button and it should turn off.

## Working modes

The remote has two modes that can be toggled by briefly pressing the button with the remote turned on. It starts by default in mode 1.

* Mode 1: Show board battery level.
* Mode 2: Show remote battery level.

When switching modes, the remote will vibrate quickly to indicate what mode you have moved to. If in mode 1, press the button for at least 250ms and you'll feel 2 short vibrations. You're now on mode 2. If in mode 2, press the button and you'll feel 1 short vibration. You're now on mode 1 again.

## Calibration mode

If you have to repeat the hall sensor calibration follow these steps:

* Make sure the remote is OFF.
* Press the button to turn it ON, but don't release it until it stops vibrating on its own and the first LED turns ON. 
* Now follow the [calibration procedure](./software.md#calibration)

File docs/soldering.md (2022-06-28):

# Assembly

## Soldering the LoRa module

The first thing to do would be to solder the LoRa module in the appropriate spot. Using solder paste and a reflow station is recommended, but the footprint has slightly oversized pads so it can be done using a regular soldering iron. It should look like this:

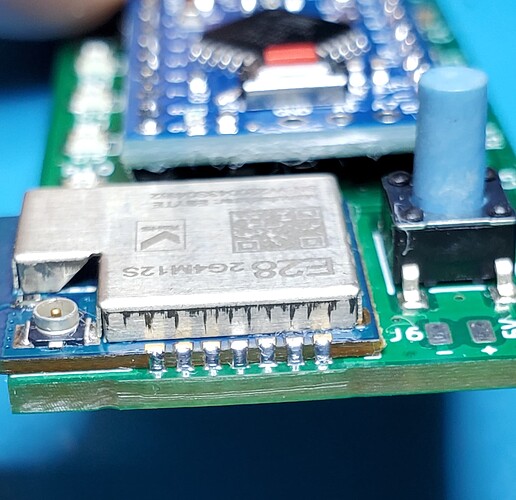
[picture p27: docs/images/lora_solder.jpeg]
Lora module


## **IMPORTANT**

Some LoRa modules come with the external antenna selected, instead of the integrated one in the PCB. This WILL cause problems, increased sensitivity to interferences and dropouts. It is very important to make sure the resistor that selects the PCB antenna is in the correct position and move it otherwise:

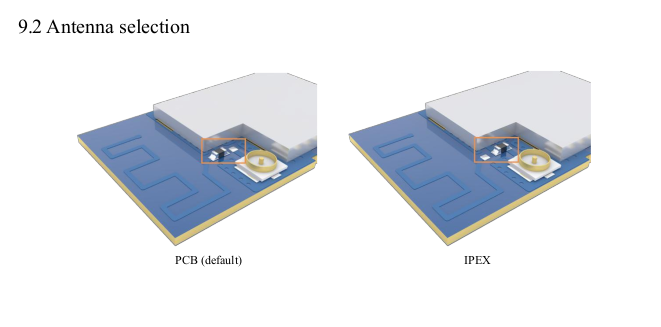
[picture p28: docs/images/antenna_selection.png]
Antenna selection


## Soldering the Arduino

Make sure you have soldered the LoRa module first! While certainly possible to do the other way around, it is a lot easier to do it in this order. Using some pin headers (that should be included in the Arduino package), solder the Arduino to the PCB, making sure the orientation is correct (programming pins next to the top of the board where the throttle pads are) and A4/A5 pins are also soldered using a 2x1 pin header. These are only needed for the transmitter, but they don't hurt anyways. The transmitter *requires* a board equipped with the more powerful Atmega 328p processor, but the receiver can use the cheaper Atmega 168.

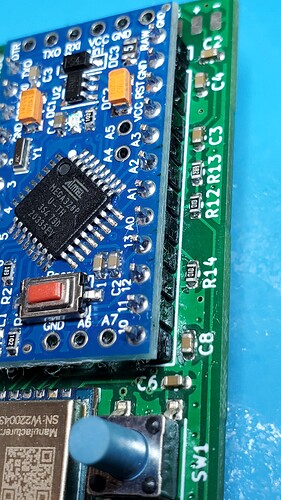
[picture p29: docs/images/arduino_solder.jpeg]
Arduino


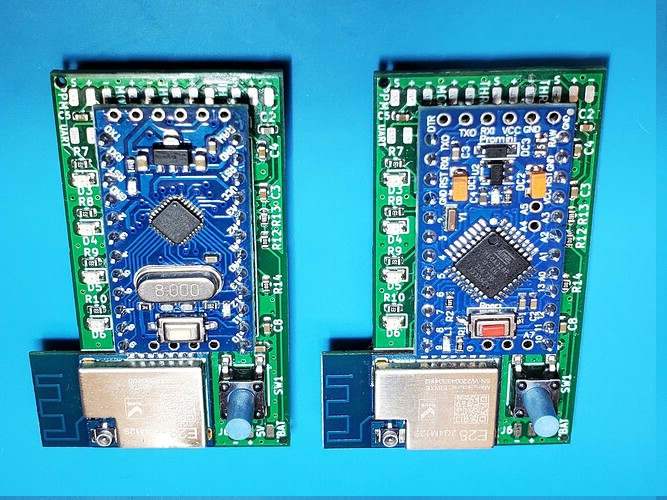
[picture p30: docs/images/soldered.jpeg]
Rx and Tx


## **IMPORTANT** 

The reset button on both Arduinos **MUST** be removed. Nobody wants their remote to reset due to a bump or squeezing too hard.

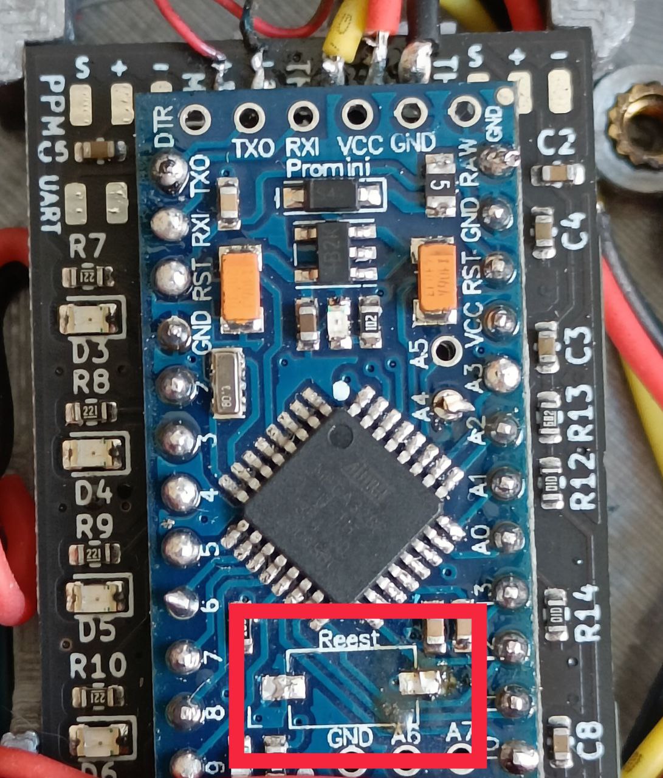
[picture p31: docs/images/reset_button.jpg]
Reset button


## Completing the transmitter circuit

All the other components should be soldered to the appropriate pads. The connections are shown in this diagram (dotted lines mean optional)

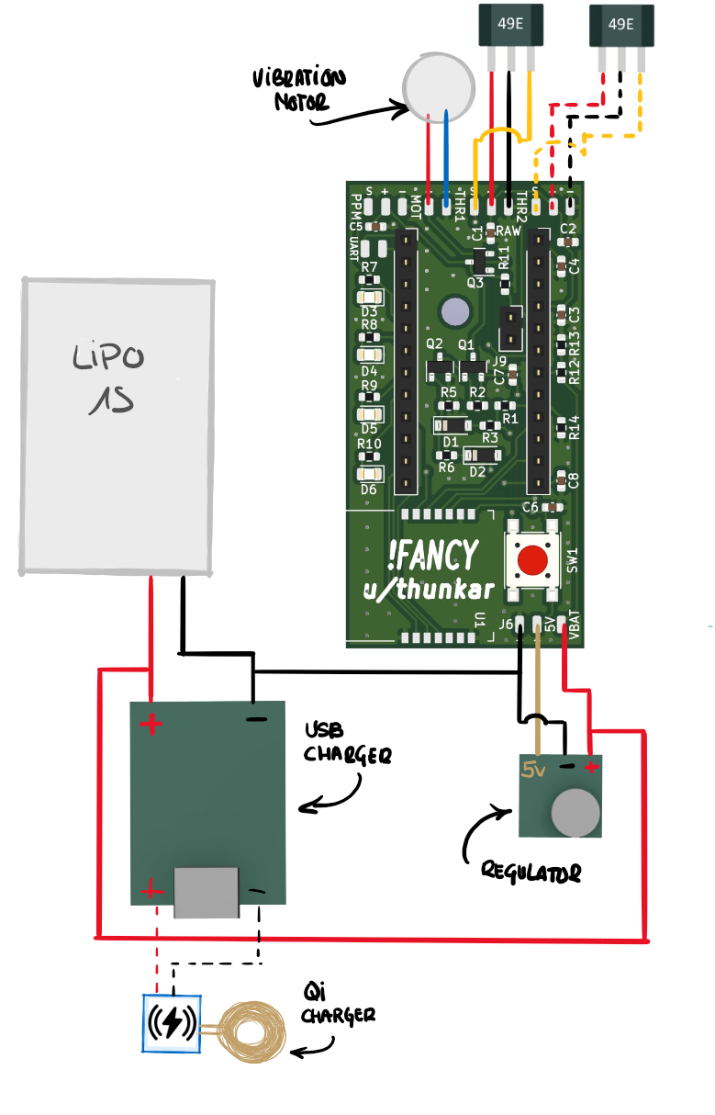
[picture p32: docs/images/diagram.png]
Diagram


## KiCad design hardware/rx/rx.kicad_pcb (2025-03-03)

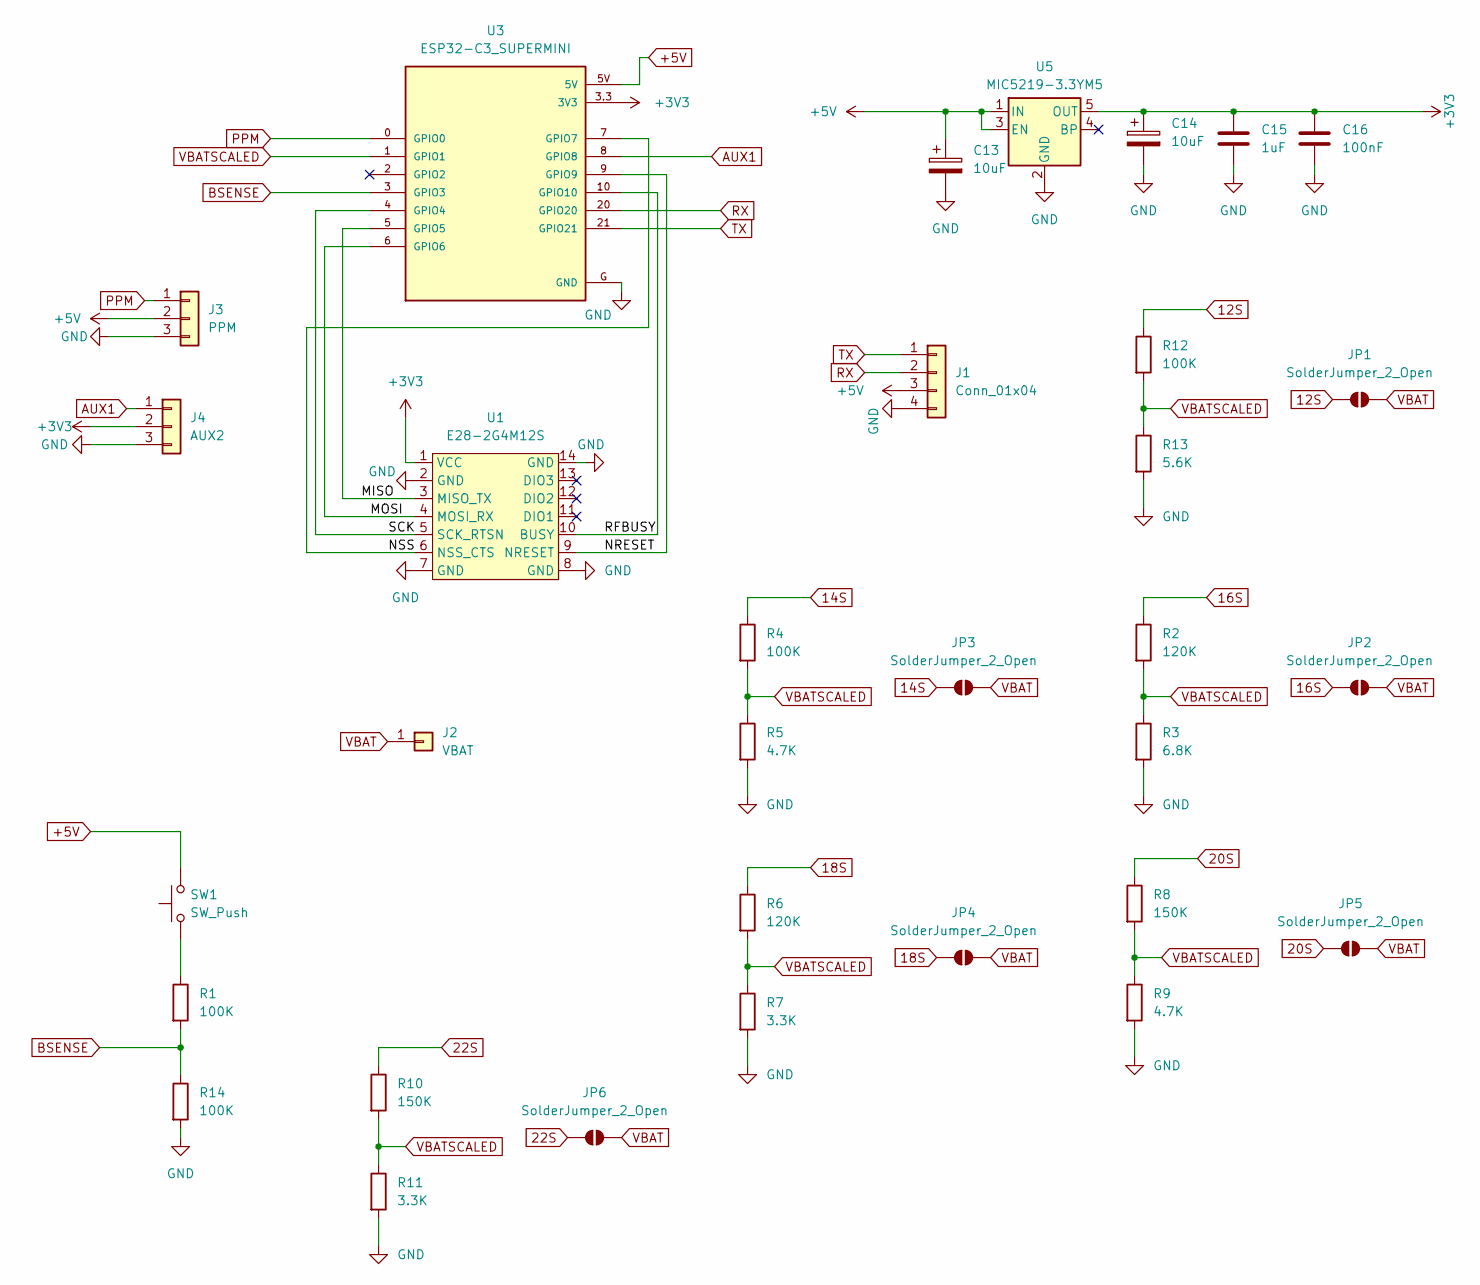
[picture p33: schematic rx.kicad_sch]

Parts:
C13, C14: 10uF; CP_EIA-3216-10_Kemet-I; LCSC C119051
C15: 1uF; C_0402_1005Metric; LCSC C52923
C16: 100nF; C_0402_1005Metric; LCSC C307331
J1: Conn_01x04; SolderWirePad_1x04_SMD_1x2mm
J2: VBAT; SolderWirePad_1x01_SMD_1x2mm
J3: PPM; SolderWirePad_1x03_SMD_1x2mm
J4: AUX2; SolderWirePad_1x03_SMD_1x2mm
JP1, JP2, JP3, JP4, JP5, JP6: SolderJumper_2_Open; SolderJumper-2_P1.3mm_Open_RoundedPad1.0x1.5mm
R1, R4, R12, R14: 100K; R_0402_1005Metric; LCSC C25741
R2, R6: 120K; R_0402_1005Metric; LCSC C25741
R3: 6.8K; R_0402_1005Metric; LCSC C407725
R5, R9: 4.7K; R_0402_1005Metric; LCSC C407725
R7, R11: 3.3K; R_0402_1005Metric; LCSC C407725
R8, R10: 150K; R_0402_1005Metric; LCSC C25741
R13: 5.6K; R_0402_1005Metric; LCSC C407725
SW1: SW_Push; SW_SPST_PTS645; LCSC C393947
U1: E28-2G4M12S
U3: ESP32-C3_SUPERMINI; MODULE_ESP32-C3_SUPERMINI
U5: MIC5219-3.3YM5; SOT-23-5; LCSC C29613

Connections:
12S: JP1.1 (A), R12.1
14S: JP3.1 (A), R4.1
16S: JP2.1 (A), R2.1
18S: JP4.1 (A), R6.1
20S: JP5.1 (A), R8.1
22S: JP6.1 (A), R10.1
+3V3: C14.1, C15.1, C16.1, J4.2, U1.1 (VCC), U3.3.3 (3V3), U5.5 (OUT)
+5V: C13.1, J1.3, J3.2, SW1.2, U3.5V, U5.1 (IN), U5.3 (EN)
/MISO: U1.3 (MISO_TX), U3.5 (GPIO5)
/MOSI: U1.4 (MOSI_RX), U3.6 (GPIO6)
/NRESET: U1.9 (NRESET), U3.9 (GPIO9)
/NSS: U1.6 (NSS_CTS), U3.7 (GPIO7)
/RFBUSY: U1.10 (BUSY), U3.10 (GPIO10)
/SCK: U1.5 (SCK_RTSN), U3.4 (GPIO4)
AUX1: J4.1, U3.8 (GPIO8)
BSENSE: R1.2, R14.1, U3.3 (GPIO3)
GND: C13.2, C14.2, C15.2, C16.2, J1.4, J3.3, J4.3, R3.2, R5.2, R7.2, R9.2, R11.2, R13.2, R14.2, U1.2 (GND), U1.7 (GND), U1.8 (GND), U1.14 (GND), U3.G (GND), U5.2 (GND)
unnamed: R1.1, SW1.1
PPM: J3.1, U3.0 (GPIO0)
RX: J1.2, U3.20 (GPIO20)
TX: J1.1, U3.21 (GPIO21)
VBAT: J2.1, JP1.2 (B), JP2.2 (B), JP3.2 (B), JP4.2 (B), JP5.2 (B), JP6.2 (B)
VBATSCALED: R2.2, R3.1, R4.2, R5.1, R6.2, R7.1, R8.2, R9.1, R10.2, R11.1, R12.2, R13.1, U3.1 (GPIO1)

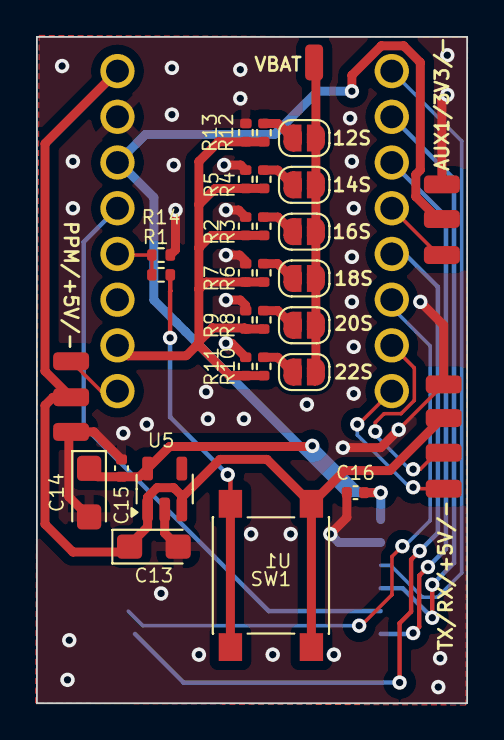
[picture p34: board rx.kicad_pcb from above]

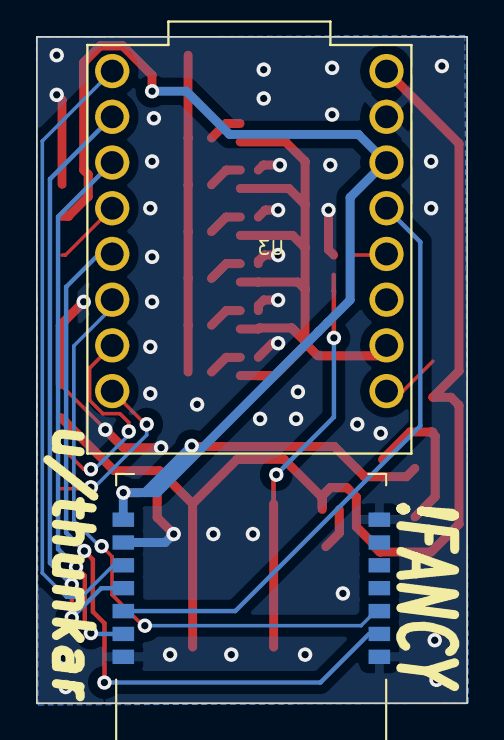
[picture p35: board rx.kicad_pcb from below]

Board: 2 copper layers, 23.9 x 37.0 mm, 32 parts (2 on the bottom side), 23 nets.

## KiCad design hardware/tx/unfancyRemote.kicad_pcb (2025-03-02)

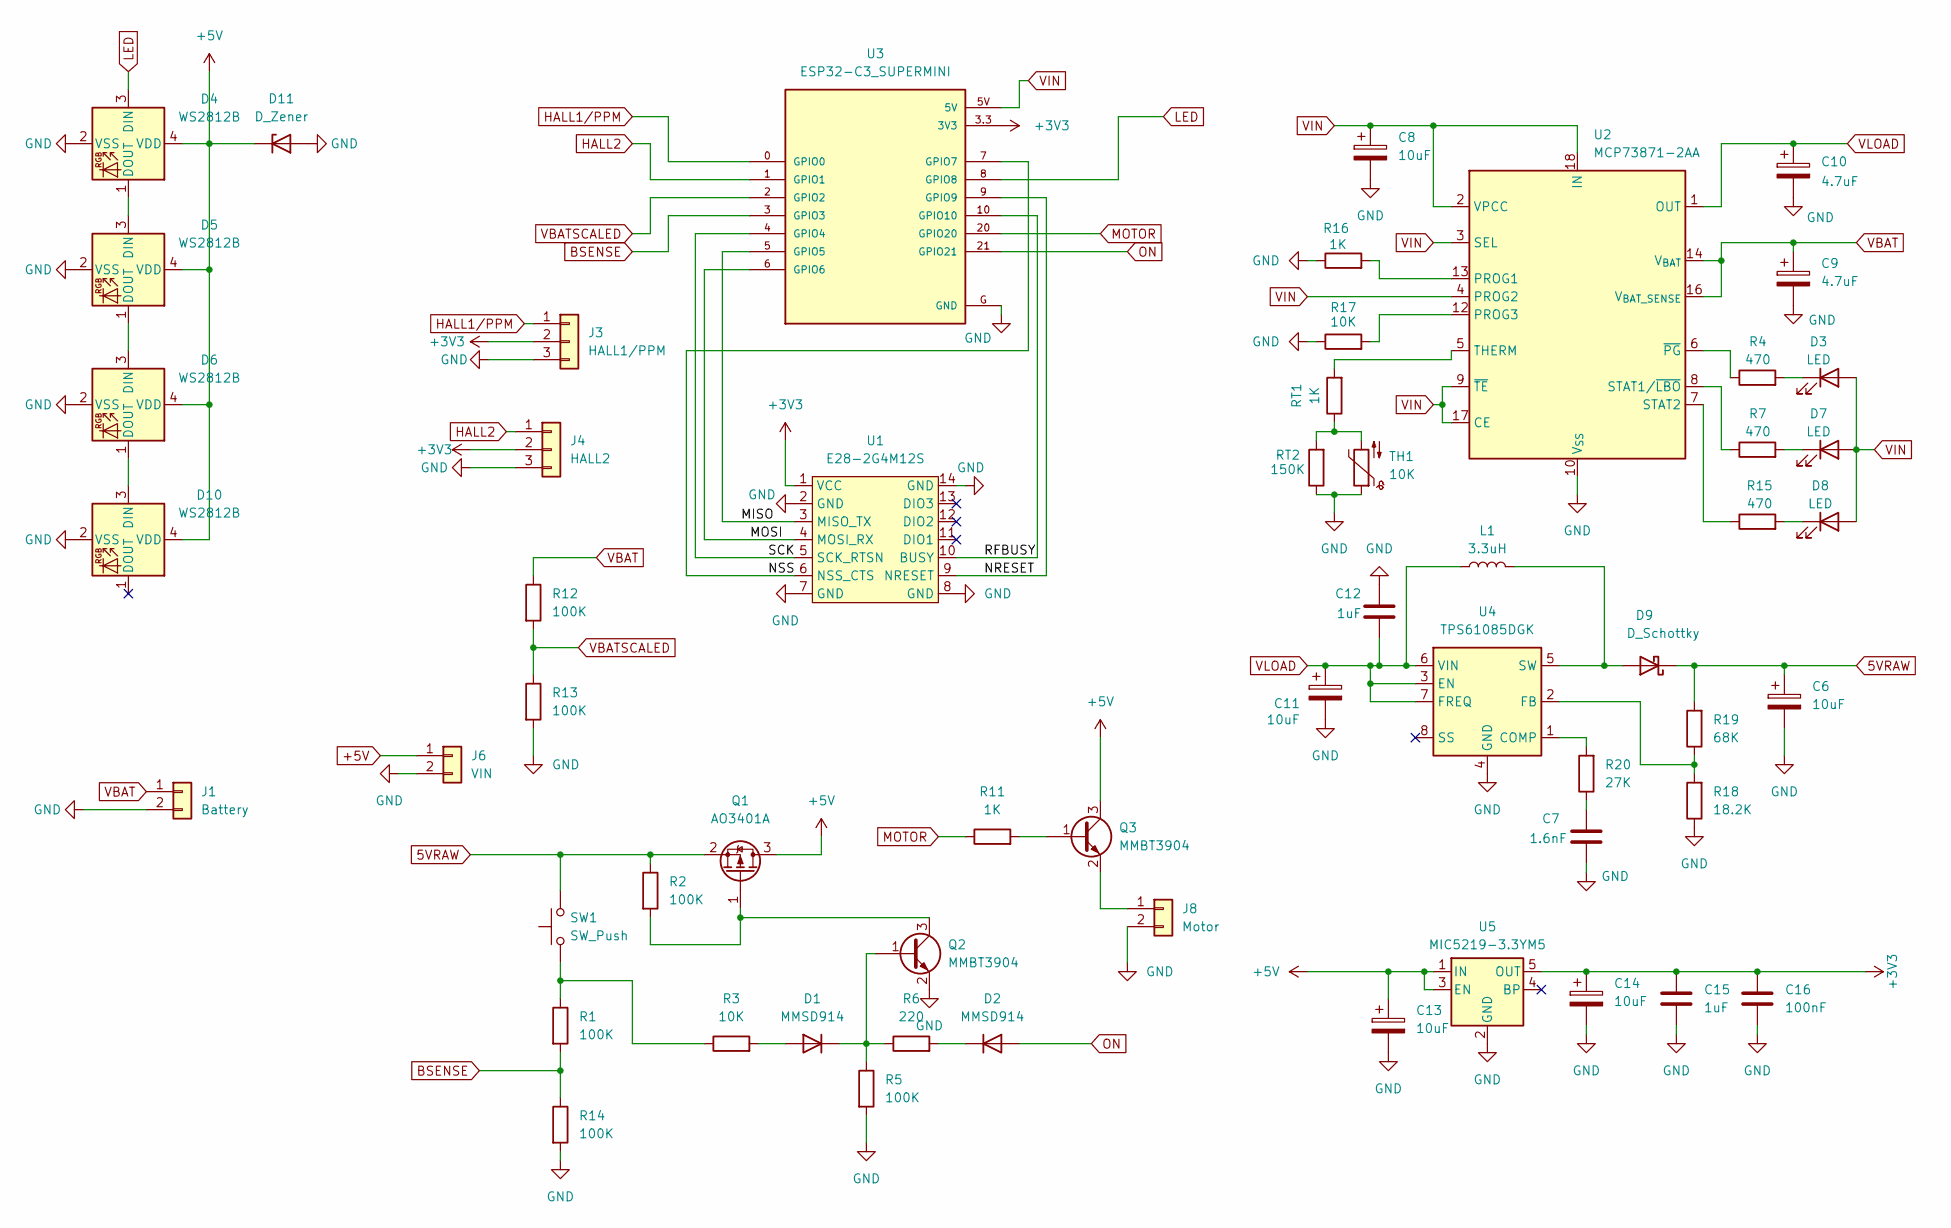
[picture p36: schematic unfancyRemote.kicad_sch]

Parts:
C6, C8, C11, C13, C14: 10uF; CP_EIA-3216-10_Kemet-I; LCSC C119051
C7: 1.6nF; C_0603_1608Metric; LCSC C437532
C9, C10: 4.7uF; CP_EIA-3216-10_Kemet-I; LCSC C123256
C12, C15: 1uF; C_0402_1005Metric; LCSC C52923
C16: 100nF; C_0402_1005Metric; LCSC C307331
D1, D2: MMSD914; D_SOD-123; LCSC C21508
D3, D7, D8: LED; LED_0805_2012Metric; LCSC C84256
D4, D5, D6, D10: WS2812B; LED_WS2812B-2020_PLCC4_2.0x2.0mm; LCSC C965555
D9: D_Schottky; D_SOD-523; LCSC C413992
D11: D_Zener; D_SOD-123
J1: Battery; PinHeader_1x02_P2.00mm_Vertical
J3: HALL1/PPM; SolderWirePad_1x03_SMD_1x2mm
J4: HALL2; SolderWirePad_1x03_SMD_1x2mm
J6: VIN; SolderWirePad_1x02_SMD_1x2mm
J8: Motor; SolderWirePad_1x02_SMD_1x2mm
L1: 3.3uH; L_Cenker_CKCS201610; LCSC C696469
Q1: AO3401A; SOT-23; LCSC C700954
Q2, Q3: MMBT3904; SOT-23; LCSC C20526
R1, R2, R5, R12, R14: 100K; R_0402_1005Metric; LCSC C25741
R3, R17: 10K; R_0402_1005Metric; LCSC C25744
R4, R7, R15: 470; R_0402_1005Metric; LCSC C25117
R6: 220; R_0402_1005Metric; LCSC C25091
R11, R16: 1K; R_0402_1005Metric; LCSC C11702
R13: 100K; R_0402_1005Metric; LCSC C407725
R18: 18.2K; R_0402_1005Metric; LCSC C25859
R19: 68K; R_0402_1005Metric; LCSC C482226
R20: 27K; R_0402_1005Metric; LCSC C284471
RT1: 1K; R_0402_1005Metric; LCSC C11702
RT2: 150K; R_0402_1005Metric; LCSC C407748
SW1: SW_Push; SW_SPST_PTS645; LCSC C393947
TH1: 10K; R_0402_1005Metric; LCSC C700818
U1: E28-2G4M12S
U2: MCP73871-2AA; QFN-20-1EP_4x4mm_P0.5mm_EP2.5x2.5mm; LCSC C144351
U3: ESP32-C3_SUPERMINI; MODULE_ESP32-C3_SUPERMINI
U4: TPS61085DGK; VSSOP-8_3x3mm_P0.65mm; LCSC C113659
U5: MIC5219-3.3YM5; SOT-23-5; LCSC C29613

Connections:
5VRAW: C6.1, D9.1 (K), Q1.2 (S), R2.1, R19.2, SW1.2
+3V3: C14.1, C15.1, C16.1, J3.2, J4.2, U1.1 (VCC), U3.3.3 (3V3), U5.5 (OUT)
+5V: C13.1, D4.4 (VDD), D5.4 (VDD), D6.4 (VDD), D10.4 (VDD), D11.1 (K), J6.1, Q1.3 (D), Q3.3 (C), U5.1 (IN), U5.3 (EN)
/MISO: U1.3 (MISO_TX), U3.5 (GPIO5)
/MOSI: U1.4 (MOSI_RX), U3.6 (GPIO6)
/NRESET: U1.9 (NRESET), U3.9 (GPIO9)
/NSS: U1.6 (NSS_CTS), U3.7 (GPIO7)
/RFBUSY: U1.10 (BUSY), U3.10 (GPIO10)
/SCK: U1.5 (SCK_RTSN), U3.4 (GPIO4)
BSENSE: R1.2, R14.1, U3.3 (GPIO3)
GND: C6.2, C7.2, C8.2, C9.2, C10.2, C11.2, C12.1, C13.2, C14.2, C15.2, C16.2, D4.2 (VSS), D5.2 (VSS), D6.2 (VSS), D10.2 (VSS), D11.2 (A), J1.2, J3.3, J4.3, J6.2, J8.2, Q2.2 (E), R5.2, R13.2, R14.2, R16.1, R17.1, R18.1, RT2.1, TH1.1, U1.2 (GND), U1.7 (GND), U1.8 (GND), U1.14 (GND), U2.10 (V_{SS}), U2.11 (V_{SS}), U2.21 (V_{SS}), U3.G (GND), U4.4 (GND), U5.2 (GND)
HALL1/PPM: J3.1, U3.0 (GPIO0)
HALL2: J4.1, U3.1 (GPIO1)
LED: D4.3 (DIN), U3.8 (GPIO8)
MOTOR: R11.1, U3.20 (GPIO20)
unnamed: C7.1, R20.1
unnamed: D1.2 (A), R3.2
unnamed: D1.1 (K), Q2.1 (B), R5.1, R6.1
unnamed: D2.1 (K), R6.2
unnamed: D3.1 (K), R4.2
unnamed: D4.1 (DOUT), D5.3 (DIN)
unnamed: D5.1 (DOUT), D6.3 (DIN)
unnamed: D7.1 (K), R7.2
unnamed: D8.1 (K), R15.2
unnamed: D9.2 (A), L1.2, U4.5 (SW)
unnamed: D6.1 (DOUT), D10.3 (DIN)
unnamed: J8.1, Q3.2 (E)
unnamed: Q1.1 (G), Q2.3 (C), R2.2
unnamed: Q3.1 (B), R11.2
unnamed: R1.1, R3.1, SW1.1
unnamed: RT1.1, RT2.2, TH1.2
unnamed: R16.2, U2.13 (PROG1)
unnamed: R17.2, U2.12 (PROG3)
unnamed: R7.1, U2.8 (STAT1/~LBO)
unnamed: R15.1, U2.7 (STAT2)
unnamed: RT1.2, U2.5 (THERM)
unnamed: R4.1, U2.6 (~PG)
unnamed: R20.2, U4.1 (COMP)
unnamed: R18.2, R19.1, U4.2 (FB)
ON: D2.2 (A), U3.21 (GPIO21)
VBAT: C9.1, J1.1, R12.1, U2.14 (V_{BAT}), U2.15 (V_{BAT}), U2.16 (V_{BAT_SENSE})
VBATSCALED: R12.2, R13.1, U3.2 (GPIO2)
VIN: C8.1, D3.2 (A), D7.2 (A), D8.2 (A), U2.2 (VPCC), U2.3 (SEL), U2.4 (PROG2), U2.9 (~TE), U2.17 (CE), U2.18 (IN), U2.19 (IN), U3.5V
VLOAD: C10.1, C11.1, C12.2, L1.1, U2.1 (OUT), U2.20 (OUT), U4.3 (EN), U4.6 (VIN), U4.7 (FREQ)

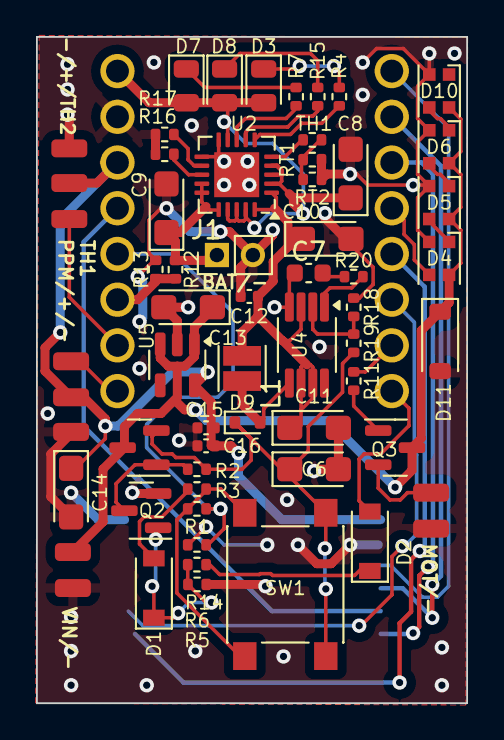
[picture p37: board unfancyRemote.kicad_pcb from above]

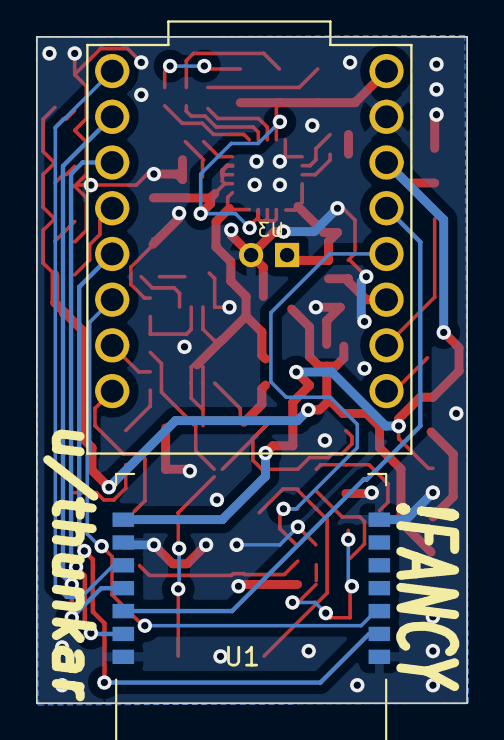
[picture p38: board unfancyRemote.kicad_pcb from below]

Board: 2 copper layers, 23.9 x 37.0 mm, 57 parts (2 on the bottom side), 44 nets.

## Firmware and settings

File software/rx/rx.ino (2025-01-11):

#include <SPI.h>
#include <SX128XLT.h>
#include "board.h"
#include "settings.h"
#include <ProgramLT_Definitions.h>
#include <Arduino.h>
#include <ESP32Servo.h> 

Servo PPM;

SX128XLT LT;

const int TASKS_LENGTH = 5;

char *taskNames[] = { "receiveThrottlePacket", "writePPMValue", "sendTMPacket", "checkBattery", "printStats" };
long periods[] = { 1, 20, 1, 1000, 2000 };
long lastRun[] = { 0, 0, 0, 0, 0 };
long executions[] = { 0, 0, 0, 0, 0 };

// const int LEDS_LENGTH = 3;

// int LEDStatus[] = { LOW, LOW, LOW };
// int storedLEDStatus[] = { LOW, LOW, LOW };
// long LEDPeriods[] = { -1, -1, -1 };
// int LEDResetCounters[] = { -1, -1, -1 };
// long lastLEDToggled[] = { 0, 0, 0 };

const unsigned int ENCODED_MAX = 65535;
const unsigned int ENCODED_HALF = 32768;
unsigned int batteryVoltage = 0;
unsigned int throttleValue = ENCODED_HALF;

volatile int RFAvailable = 1;
volatile int interruptCounter = 1;
bool forceRX = true;

bool error = false;
int errors = 0;
char errorReason[30];
long currentRSSI = -100;
int currentSNR = -100;
unsigned long frequency;

unsigned long packets = 0;
unsigned long TMPackets = 0;
unsigned int TMRequest = 0;
bool waitingForRX = false;
unsigned int maxWaitForReceive = 250;
unsigned int currentReceiveCycles = 0;

int VCC = 0;

#define DEBUG
//#define DEBUG_FLAGS

void printFlags(char title[]) {
  Serial.print(title);
  Serial.print(F(" | ThrottleValue: "));
  Serial.print(throttleValue);
  Serial.print(F(" | RFAvailable: "));
  Serial.print(RFAvailable);
  Serial.print(F(" | TMRequest: "));
  Serial.println(TMRequest);
}

int readVcc(void) {
   int result = 0;
   return result; // Vcc in millivolts
}

void clearError() {
  error = false;
}

void setError(char reason[]) {
  errors++;
  error = true;
  strcpy(errorReason, reason);
}

// void ONSequence() {
//     for(int i = LEDS_LENGTH-1; i > -1; i--) {
//       digitalWrite(LEDPins[i], HIGH);
//       delay(100);
//     }
//     delay(100);
//     for(int i = 0; i < LEDS_LENGTH; i++) {
//       digitalWrite(LEDPins[i], LOW);
//       delay(50);
//     }
//     VCC = readVcc();
// }

// void setLEDOn(int LEDn) {
//   LEDPeriods[LEDn] = 0;
//   LEDResetCounters[LEDn] = -1;
// }

// void setLEDOff(int LEDn) {
//   LEDPeriods[LEDn] = -1;
//   LEDResetCounters[LEDn] = -1;
// }

// void flashLED(int LEDn, int times, unsigned long period, int resetStatus) {
//   LEDPeriods[LEDn] = period;
//   LEDResetCounters[LEDn] = times;
//   storedLEDStatus[LEDn] = resetStatus;
// }

bool checkBattery(unsigned long now) {
  int batValue = analogRead(VBAT);
  int scaledBatmVolts = map(batValue, 0, 1023, 0, VCC);
  float newBatteryVoltage = (scaledBatmVolts/1000.0)*(R1+R2)/R2;
  batteryVoltage = batteryVoltage != -1 ? (newBatteryVoltage + batteryVoltage) / 2 : newBatteryVoltage;
  return true;
}

void IRAM_ATTR processRFInterrupt() {
  RFAvailable = !digitalRead(RFBUSY);
  interruptCounter++;
}

void processReceivedPacket() {
  clearError();
  if(!checkRXIRQError()) {
    setError("IRQ Error");
    return;
  }                                               
  unsigned int TXIdentity = -1;
  unsigned int receivedValue = ENCODED_HALF;
  unsigned int receivedTMRequest = 0;
  unsigned int measuredRXPacketLength = LT.readRXPacketL();
  int measuredSNR = 0;
  long measuredRSSI = 0;
  
  if(measuredRXPacketLength == throttlePacketLength){
    LT.startReadSXBuffer(0);                
    TXIdentity = LT.readUint8();         
    receivedValue = LT.readUint16();       
    receivedTMRequest = LT.readUint8();
    LT.endReadSXBuffer(); 
    measuredRSSI = LT.readPacketRSSI();      
    measuredSNR = LT.readPacketSNR(); 
       
    if(TXIdentity != RXIdentity) {
      char reason[30];
      sprintf(reason, "Incorrect identity %3d", TXIdentity);
      setError(reason);
    }
  } else {
    char reason[30];
    sprintf(reason, "Incorrect packet length %3d", measuredRXPacketLength);
    setError(reason);
  }
  
  if(!error) {
    packets++;
    currentSNR = measuredSNR;
    currentRSSI = measuredRSSI;
    throttleValue = receivedValue;
    TMRequest = receivedTMRequest;
  }
}

bool checkTXRXDone() {
  uint16_t IRQStatus = LT.readIrqStatus();
  bool done = (IRQStatus & 0x4022 ) || (IRQStatus & 0x4001);   //IRQs going active
  return done;
}

bool checkRXIRQError() {
  uint16_t IRQStatus = LT.readIrqStatus();
  return !(IRQStatus & (IRQ_HEADER_ERROR + IRQ_CRC_ERROR + IRQ_RX_TX_TIMEOUT + IRQ_SYNCWORD_ERROR));
}

bool sendTMPacket(unsigned long now) {
  if(!TMRequest || !RFAvailable || !checkTXRXDone()) {
    return false;
  }
  LT.startWriteSXBuffer(0);                     
  LT.writeUint8(RXIdentity);                    
  LT.writeUint16(batteryVoltage);                        
  LT.endWriteSXBuffer();   
  #ifdef DEBUG_FLAGS                 
  printFlags("Transmit");
  #endif
  LT.transmitSXBufferIRQ(0, TMPacketLength, 0, TXpower, NO_WAIT);  
  TMPackets++;
  TMRequest = 0;
  return true;
}

bool receiveThrottlePacket(unsigned long now) {
  if(TMRequest) {
    currentReceiveCycles = 0;
    return false;
  }
  // Excluding tm receives, we have been waiting for more than 50ms for a throttle packet. Reset everything and try again!
  if(currentReceiveCycles >= maxWaitForReceive/periods[0]) { 
    currentReceiveCycles = 0;
    waitingForRX = false;
    forceRX = true;
    TMRequest = 0;
    currentSNR = -100;
    currentRSSI = -100;
    throttleValue = ENCODED_HALF;
    setError("Receive timeout");
    LT.config();
    return false;
  }
  if((!checkTXRXDone() || !RFAvailable) && !forceRX) {
    currentReceiveCycles++;
    return false;
  }
  forceRX = false;
  if(!waitingForRX) {
    waitingForRX = true;
    #ifdef DEBUG_FLAGS  
    printFlags("Receive");
    #endif
    LT.receiveSXBufferIRQ(0, 0, NO_WAIT);
    return false;
  } else {
    #ifdef DEBUG_FLAGS   
    printFlags("Process throttle");
    #endif
    processReceivedPacket();
    currentReceiveCycles = 0;
    waitingForRX = false;
    return true;
  }
}

bool writePPMValue(unsigned long now) {
  unsigned int throttlePulse = map(throttleValue, 0, ENCODED_MAX, 1000, 2000);
  PPM.writeMicroseconds(throttlePulse);
  return true;
}

// bool setLEDs(unsigned long now) {
//   for(int i = 0; i < LEDS_LENGTH; i++) {
//     int currentStatus = LEDStatus[i];
//     if(LEDPeriods[i] == -1) {
//       LEDStatus[i] = LOW;
//     } else if(LEDPeriods[i] == 0) {
//       LEDStatus[i] = HIGH;
//     } else if(now - lastLEDToggled[i] >= LEDPeriods[i]) {
//       int isBlinking = LEDResetCounters[i] != 0;
//       if(isBlinking) {
//         LEDStatus[i] = !LEDStatus[i];
//         if(LEDStatus[i] && LEDResetCounters[i] > 0) {
//           LEDResetCounters[i]--;
//         }
//         lastLEDToggled[i] = now;
//       } else {
//         storedLEDStatus[i] ? setLEDOn(i) : setLEDOff(i);
//       }
//     }
//     if(currentStatus != LEDStatus[i]) {
//       digitalWrite(LEDPins[i], LEDStatus[i]);
//     }
//   }
//   return true;
// }


bool printStats(unsigned long now) {
  #ifdef DEBUG
  if(errors > 0) {
    Serial.println(F("////////ERROR//////////"));
    Serial.println(errorReason);
    Serial.println(F("//////////////////////"));
  }
  Serial.print(F("Frequency: "));
  Serial.print(frequency);
  Serial.println(F("Hz"));
  float ellapsed = (now - lastRun[TASKS_LENGTH-1])/1000;
  Serial.print(F("Ellapsed: "));
  Serial.print(ellapsed);
  Serial.print(F("s | VBat: "));
  Serial.print(batteryVoltage/1000.0);
  Serial.print(F("V | SNR: "));
  Serial.print(currentSNR);
  Serial.print(F("dB | RSSI: "));
  Serial.print(currentRSSI);
  Serial.println(F("dBm"));
  Serial.println(F("-------------- TASKS --------------"));
  for(int i = 0; i < TASKS_LENGTH - 1; i++) {
    char prBuffer[45];
    int frequency = round(executions[i] / ellapsed);
    sprintf(prBuffer, "%-23s | %5dHz", taskNames[i], frequency);
    Serial.print(prBuffer);
    Serial.println("");
    executions[i] = 0;
  }
  Serial.println(F("-----------------------------------"));
  int packetsPerSecond = round(packets / ellapsed);
  Serial.print(F("Packets/s: "));
  Serial.println(packetsPerSecond);
  int TMPacketsPerSecond = round(TMPackets / ellapsed);
  Serial.print(F("TM packets/s: "));
  Serial.println(TMPacketsPerSecond);
  Serial.print(F("Errors: "));
  Serial.println(errors);
  errors = 0;
  packets = 0;
  TMPackets = 0;
  #endif
  return true;
}

typedef bool (*task)(unsigned long);

task tasks[] = { receiveThrottlePacket, writePPMValue, sendTMPacket, checkBattery, printStats };

void loop()
{
  for(int i = 0; i < TASKS_LENGTH; i++) {
    unsigned long now = millis();
    if(now - lastRun[i] >= periods[i]) {
      if(tasks[i](now)) {
        executions[i]++;
      }
      lastRun[i] = millis();
    }
  }
}


void setup()
{
  pinMode(PPM_THR1, OUTPUT);
  pinMode(LED, OUTPUT);
 // ONSequence();
  attachInterrupt(RFBUSY, processRFInterrupt, CHANGE);
  PPM.attach(PPM_THR1);

  #ifdef DEBUG
  Serial.begin(115200);
  #endif

  SPI.begin();

  if (!LT.begin(NSS, NRESET, RFBUSY, LORA_DEVICE))
  {
    #ifdef DEBUG
    Serial.println(F("Device error"));
    #endif
  }

  frequency = channel * CH_BANDWIDTH_HZ + BASE_FREQUENCY;
  LT.setupLoRa(frequency, Offset, SpreadingFactor, Bandwidth, CodeRate);
  LT.clearIrqStatus(IRQ_RADIO_ALL);
  
  #ifdef DEBUG
  Serial.println(F("Receiver ready"));
  #endif
}

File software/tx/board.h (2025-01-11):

//*******  Setup hardware pin definitions here ! ***************

const int NSS = 7;                           //select on LoRa device
const int NRESET = 9;                        //reset on LoRa device
const int RFBUSY = 10;                        //RF busy on LoRa device 
const int DIO1 = -1;                          //DIO1 on LoRa device, used for RX and TX done
const int DIO2 = -1;                         //DIO2 on LoRa device, normally not used so set to -1
const int DIO3 = -1;                         //DIO3 on LoRa device, normally not used so set to -1
const int RX_EN = -1;                        //pin for RX enable, used on some SX1280 devices, set to -1 if not used
const int TX_EN = -1;                        //pin for TX enable, used on some SX1280 devices, set to -1 if not used

const int ON = 21;
const int BUTTON = 3;
const int PPM_THR1 = 0;
const int LED = 8;
const int MOTOR = 20;
const int VBAT = 2;
const int THR2 = 1;

const unsigned long R2 = 6800;
const unsigned long R1 = 100000;


//*******  Setup LoRa Test Parameters Here ! ***************


#define LORA_DEVICE DEVICE_SX1280    
#define Offset 0                                 //offset frequency for calibration purposes  
#define Bandwidth LORA_BW_1600                   //LoRa bandwidth
#define SpreadingFactor LORA_SF7                 //LoRa spreading factor
#define CodeRate LORA_CR_4_5                     //LoRa coding rate
#define CH_BANDWIDTH_HZ 2500000
#define BASE_FREQUENCY 2400000000

const unsigned int throttlePacketLength = 4;                  //packet length is fixed 
const unsigned int TMPacketLength = 3;
const unsigned int TXpower = 10;                       //LoRa transmit power in dBm

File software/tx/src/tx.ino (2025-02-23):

#include <Arduino.h>
#include <SPI.h>
#include "soc/soc.h"
#include "soc/rtc_cntl_reg.h"
#include "board.h"
#include "settings.h"
#include "state.h"
#include "RF.h"
#include "mode.h"
#include "button.h"
#include "throttle.h"
#include "LED.h"
#include "motor.h"
#include "battery.h"
#include "wifi_setup.h"
#include "error_handling.h"


int LAST_TASK;
int FIRST_TASK;

char *taskNames[] = { "sendThrottlePacket", "receiveTMPacket", "readThrottle", "checkButton", "checkBattery", "displayMode", "setLEDs", "setMotor", "printStats", "doServerWork" };
unsigned long lastRun[] = { 0, 0, 0, 0, 0, 0, 0, 0, 0, 0 };
unsigned long executions[] = { 0, 0, 0, 0, 0, 0, 0, 0, 0, 0 };


#define DEBUG

void ONSequence() {
    for(int i = LEDS_LENGTH-1; i > -1; i--) {
      LEDColor[i] = rainbow[i];
      FastLED.show();
      delay(100);
    }
    digitalWrite(ON, HIGH);
    delay(100);
    digitalWrite(MOTOR, HIGH);
    delay(100);
    unsigned long now = millis();
    unsigned long lastCheck = now;
    while(digitalRead(BUTTON)){
      state.setupMode = (lastCheck - now) > setupModeDelay;
      lastCheck = millis();
      if(state.setupMode) {
        break;
      }
    };
    digitalWrite(MOTOR, LOW);
    for(int i = 0; i < LEDS_LENGTH; i++) {
      LEDColor[i] = CRGB::Black;
      FastLED.show();
      delay(50);
    }
}

bool printStats(unsigned long now) {
  #ifdef DEBUG
  if(state.errors > 0) {
    Serial.println(F("////////ERROR//////////"));
    Serial.println(state.errorReason);
    Serial.println(F("//////////////////////"));
  }
  float ellapsed = (now - lastRun[8])/1000;
  Serial.print(F("Ellapsed: "));
  Serial.print(ellapsed);
  Serial.print(F("s | VBat: "));
  Serial.print(state.batteryVoltage);
  Serial.print(F("V | Mode: "));
  Serial.println(state.currentDisplayMode);
  Serial.print(F("Frequency: "));
  Serial.print(frequency);
  Serial.println(F("Hz"));
  Serial.print(F("SNR: "));
  Serial.print(state.currentSNR);
  Serial.print(F("dB | RSSI: "));
  Serial.print(state.currentRSSI);
  Serial.print(F("dBm | Board V: "));
  Serial.print(state.boardVoltage);
  Serial.print(F(" ("));
  Serial.print(state.boardCellVoltage);
  Serial.println(F(")"));
  Serial.print(F("Calibration: "));
  Serial.print(config.calBrake);
  Serial.print(F(" | "));
  Serial.print(config.centerAcc);
  Serial.print(F(" | "));
  Serial.print(config.calAcc);
  Serial.print(F(" | Inverted: "));
  Serial.println(config.inverted ? "y" : "n");
  Serial.println(F("-------------- TASKS --------------"));
  for(int i = FIRST_TASK; i <= LAST_TASK; i++) {
    char prBuffer[45];
    float frequency = executions[i] / ellapsed;
    sprintf(prBuffer, "%-20s | %.2fHz", taskNames[i], frequency);
    Serial.print(prBuffer);
    Serial.println("");
    executions[i] = 0;
  }
  Serial.println(F("-----------------------------------"));
  int packetsPerSecond = round(state.packets / ellapsed);
  Serial.print(F("Packets/s: "));
  Serial.println(packetsPerSecond);
  int TMPacketsPerSecond = round(state.TMPackets / ellapsed);
  Serial.print(F("TM packets/s: "));
  Serial.println(TMPacketsPerSecond);
  int interruptsPerSecond = round(state.interruptCounter / ellapsed);
  Serial.print(F("Interrupts/s: "));
  Serial.println(interruptsPerSecond);
  Serial.print(F("Errors: "));
  Serial.println(state.errors);
  state.errors = 0; 
  state.packets = 0;
  state.TMPackets = 0;
  state.interruptCounter = 0;
  #endif
  return true;
}

typedef bool (*task)(unsigned long);

task tasks[] = { sendThrottlePacket, receiveTMPacket, readThrottle, checkButton, checkBattery, displayMode, setLEDs, setMotor, printStats, doServerWork };

void loop() {
  LAST_TASK = state.setupMode ? 9 : 8;
  FIRST_TASK = state.setupMode ? 2 : 0; 
  for(int i = FIRST_TASK; i <= LAST_TASK; i++) {
    unsigned long now = millis();
    if(now - lastRun[i] >= periods[i]) {
      if(tasks[i](now)) {
        executions[i]++;
      }
      lastRun[i] = millis();
    }
  }
}


void setup() {
  WRITE_PERI_REG(RTC_CNTL_BROWN_OUT_REG, 0); //disable brownout detector

  EEPROM.begin(18);
  readConfig();
  readCalibration();
  FastLED.addLeds<WS2812B, LED, GRB>(LEDColor, LEDS_LENGTH);
  FastLED.setBrightness(128);
  FastLED.show();
  pinMode(PPM_THR1, INPUT);
  pinMode(ON, OUTPUT);
  pinMode(MOTOR, OUTPUT);
  pinMode(BUTTON, INPUT);
  ONSequence();
  
  #ifdef DEBUG
  Serial.begin(115200);
  #endif

  if(state.setupMode) {
    if(!SPIFFS.begin(true)){
      Serial.println(F("An Error has occurred while mounting SPIFFS"));
      return;
    }
    WiFi.softAP("Unfancy Remote");
    setupServer();
    #ifdef DEBUG
    Serial.println(F("Setup mode"));
    #endif
  } else {
    attachInterrupt(RFBUSY, processRFInterrupt, CHANGE);

    SPI.begin();

    if (!LT.begin(NSS, NRESET, RFBUSY, DIO1, DIO2, DIO3, RX_EN, TX_EN, LORA_DEVICE))
    {
      #ifdef DEBUG
      Serial.println(F("Device error"));
      #endif
    }

    LT.setupLoRa(frequency, Offset, SpreadingFactor, Bandwidth, CodeRate);
    LT.clearIrqStatus(IRQ_RADIO_ALL);

    #ifdef DEBUG
    Serial.println(F("Remote ready"));
    #endif
  }

 
}

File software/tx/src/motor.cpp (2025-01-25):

#include "motor.h"

int motorStatus = LOW;
unsigned long motorPeriod = -1;
unsigned long lastMotorToggled = 0;
int motorResetCounter = -1;

void pulseMotor(int times, unsigned long period) {
  motorPeriod = period;
  motorResetCounter = times;
}

bool setMotor(unsigned long now) {
  int currentStatus = motorStatus;
  if(motorPeriod == -1) {
    motorStatus = LOW;  
  } else if (motorPeriod == 0) {
    motorStatus = HIGH;
  } else if (now - lastMotorToggled >= motorPeriod) {
    int isPulsing = motorResetCounter != 0;
    if(isPulsing) {
      motorStatus = !motorStatus;
      if(motorStatus && motorResetCounter > 0){
        motorResetCounter--;
      }
      lastMotorToggled = now;
    } else {
      motorResetCounter = -1;
      motorPeriod = -1;
    }
  }
  if(currentStatus != motorStatus) {
    digitalWrite(MOTOR, motorStatus);
  }
  return true;
}

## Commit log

2022-02-25 Added kicad project for prototype hw
    [BOM-unfancyRemote.csv, bom.xls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]
2022-02-27 Fixed R and Cs footprint
    [BOM-unfancyRemote.csv, bom.xls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]
2022-03-06 Added dual trigger version
    [case.f3d, case.stl, dualTriggerBase v36.f3d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]
2022-03-09 Power button support in sw
2022-03-09 WIP 1.0
    [unfancyRemote.kicad_pcb]
2022-03-09 Updated LoRa footprint
    [thumbwheel.stl, thumbwheelBase.stl, unfancyRemote.kicad_pcb]
2022-03-10 Updates to PCB v1.0, simple disconnect detection on the remote
    [unfancyRemote.kicad_pcb]
2022-03-19 Added library, PCB 1.0, software scheduler
    [unfancyRemote.kicad_pcb, unfancyRemote.kicad_sch]
2022-03-20 Updated thumbwheel design
    [thumbwheel v9.f3d, thumbwheel.stl, thumbwheelBase v52.f3d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]
2022-03-22 Software v1.0 for rx and tx
    [unfancyRemote.kicad_pcb]
2022-03-23 Fixes and rudimentary TM
    [board.h, rx.ino, settings.h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]
2022-03-27 Software V1 with TM and failsafe
    [board.h, rx.ino, settings.h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]
2022-03-28 WIP thumbwheel case v1
    [thumbwheel.stl, thumbwheelBase.stl, thumbwheelTop.stl]
2022-04-01 Fixed rx, beefier case
    [buttonCap.stl, thumbwheelTop.stl]
2022-04-02 Improved transmission stability
    [buttonCap.stl, thumbwheelTop.stl, unfancyRemote.kicad_pcb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]
2022-04-04 Round version, PCB 2.0
    [hook.stl, roundBase.stl, thumbwheelSmall.stl]
2022-04-11 PCB improvements, round version, cal procedure
    [hook.stl, roundBase.stl, roundTop.stl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]
2022-04-18 rx string to program memory
    [roundBase.stl, roundTop.stl]
2022-04-27 Dual trigger support and better calibration
2022-04-29 CAD dump of all versions
    [dualTriggerBase v36.f3d, dualTriggerBase.f3d, dualTriggerBase.step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]
2022-05-02 Added BOM
2022-05-09 Channel implementation
    [dualTriggerBase.stl, dualTriggerTop.stl, reverseTrigger.stl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]
2022-05-10 Updated CAD files, added misc, updated BOM, basic pairing
    [PCB.f3d, PCB.step, battery.f3d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]
2022-05-12 Code cleanup, avoid overflow
    [rx.ino, settings.h, tx.ino]
2022-05-14 Added PCBv2 model
    [PCBv2.f3d, PCBv2.step]
2022-05-15 PCB v2 gerber and bom
    [BOM-unfancyRemote.csv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]
2022-06-15 Preparing sw compatibity with pcb v2
    [thumbwheelBase.stl]
2022-06-16 Updated for PCB v2
    [thumbwheelBase.stl]
2022-07-03 Completed first version of documentation
    [roundBase.stl, roundTop.stl]
2022-07-16 Hopefully squashed lock bug
    [rx.ino, tx.ino]
2022-07-16 Improved connection stability and tx/rx handover
    [rx.ino, tx.ino]
2022-08-17 CAD dump
    [PCBv2 v2.f3d, dualTriggerBase.f3d, dualTriggerBase.step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]
2022-08-17 Removed unnecesary file
    [PCBv2 v2.f3d]
2022-08-23 Force mode change on low remote battery, safer thresholds
2023-07-26 Added battery measurement average (2 samples)
2024-07-26 wip, kicad v8
    [unfancyRemote.kicad_pcb, unfancyRemote.kicad_sch]
2024-10-27 finished charging ic wiring
    [unfancyRemote.kicad_sch]
2024-11-18 power progress
    [unfancyRemote.kicad_pcb, unfancyRemote.kicad_sch]
2024-11-25 more routing
    [unfancyRemote.kicad_pcb, unfancyRemote.kicad_sch]
2025-01-25 software progress
    [PCBv3.step, unfancyRemote.kicad_pcb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]
2025-02-22 ready for calibration
2025-02-23 progress in calibration
2025-03-01 cleanup hw
    [BOM-unfancyRemote.csv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]
2025-03-01 rx PCB
    [rx.kicad_pcb, rx.kicad_sch]
2025-03-02 update to kicad 9
    [calc.xlsx, rx.kicad_pcb, rx.kicad_sch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]
2025-03-03 rx improvements
    [rx.kicad_pcb]
